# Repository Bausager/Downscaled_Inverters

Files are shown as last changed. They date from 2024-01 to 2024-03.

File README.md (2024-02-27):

# Downscaled three-phase half-bridge inverter
This project is an inverter framework for students and researches to learn, test and research state-of-the-art phase-lock-loops and control algorithms.
The inverters manly uses jellybean components, found free at the electronic laboratory for electrical engineers at Aarhus University(AU) for their students.
The purpose is to make an inexpensive and save platform instead of having to work with line voltages. 
This means all the components can be downscaled to work with 5 volt.
Here the inverter can be powered by a USB and supply its own grid.

This is an accumulative project, this means it's going to improve over time. 
There's a limited number of people working on this which means updates somethimes takes sometime.
If you want to help improve, collaborate or have something in your back pocket you want to integrate, you are very welcome to contact me!
The more the merrier!

There're some restrictions!
Since this is an open-source, student use it and research need to be understood and replicated, the code needs to be written in such a way that other prople can understand it.
Even if the person isn't an expert.
That is importent!

New fueatures waiting to be implemented can be found on the github project site [Not a Generator (NaG)](https://github.com/users/Bausager/projects/2)

## University Teaching

### Phase-Lock-Loop(PLL)
Many students at AU before this project have worked in PLLs for their bachelor thesis that meant a large part of the project was making an inverter from scratch.
This allows students not to reinvent the wheel if they are interested in other aspects than the hardware side.
With this the students can generate the grid and test their PLL on the some PCB, which lowest the bar of entre and in turn makes student projects and bachelor thesis more focused.

### Control
The students have the ability to develop control methods and test it only with a one inverter and output impedances.
Here different filter configuration or switching methods can also influence the THD which the students new have a direct way to interacting with.

### Power Factor Correction(PFC)
This PCB also allows to make it work as a PFC where control, THD and other aspects can be looked into.
Here a PFC input with a inverter output can also be pursued.

## Research Projects
Even if grid impedances does not downscale well, control algorithms, stability and many other advanced concept can be tested.
In the future, a new version of the PCB will be made for increasing the DC Link voltage to accommodate some of the downsides of the downscaled grid impedances.
As the time of writing the increase of DC Link voltage would be around 24V.
Now multiply inverters can be chained to a common grid to research stability.
Here the goal is not only to use the same micro-controller and control but to use different kinds of controls, PLLs, micro-controller, changing grid impedances, short-circuits and much more.
This will also include black start, synchronisation and much more.

## Collaborators
This project was initially an idea developed under [Associate Professor Uffe Jakobsen](https://pure.au.dk/portal/en/persons/uja%40ece.au.dk) for his classes and research into inverter control.
He also has students doing their project and bachelor thesis helping expand on this project.

A contributor [Christian Lind Vie Madsen](https://www.linkedin.com/in/christian-karl-oscar-lind-vie-madsen-11606a9b/) helps optimising written code for better performance.

And project maintainer- Me! [Michelle Bausager](https://www.linkedin.com/in/michelle-bausager/) A former student and research assistance at AU who likes to work with all aspects of inverters.

## Git Workflow.
For students or others who want to contribute, a workflow is needed to make sure everything still works in the end.
main.c on the main branch is written in such a way that every function is implementet but commented out.
This means there's a funtional implementation of every feature avaliable ready to use.

To make sure the workflow is allined a smal guide it here presented;

### Download the repository and work on an existing branch
Create of find a folder for the Git project and open your terminal in that folder.
Grab the git link and use the following git commands to download the project
```
git clone https://github.com/Bausager/Downscaled_Inverters.git
```
It’s good practice to get an overview of the project, especially the branches.
It's also here you would start if you come back to code some more!
```
git pull
git branch -a
```
There’s probably a need to code in a specific branch, if you're not in the right branch you need to select it from the list. 
Now you need to update it localy as follows:
```
git checkout specific_branch
git pull origin specific_branch
```
You can now start to make changes to the code!
To commit it, firstly you need to make sure the branch is up to date.
Then the "git add -A" commits all files and now you have to write some comments on the changes you made
Now you can push it to git!
```
git pull origin specific_branch
git add -A
git commit -m "Head line for changes
>
>
> Discription of what has been done "
git push origin specific_branch
```

### Make a new branch
Firstly make sure you have been invited to be a contributor.
Then starting working on a new feature first pull from the main branch
```
git pull origin main
```
Now you need to create a new branch where you can make your new implementations. Remember to give it a valuable name, such as "UltraCoolNewPLL".
After creating it you need to be in ýour new branch, with the opteration "checkout".
```
git branch new_branch
git checkout new_branch
```
You can now start to make changes to the code!
Since it's a new branch you don't need to make sure it's already updated as you do after you've commitet the branch for the first time.
Then the "git add -A" commits all files and now you have to write some comments on the changes you made.
```
git add -A
git commit -m "Head line for changes
>
>
> Discription of what has been done "
```
First time pushing a new branch you need to push it like this
```
git push -u origin new_branch
```
After that you can simply go to the workflow presented in *Download the repository and work on an existing branch*

### Marge branch to main
When the feature is done and tested, it's time to merge with the main branch.
This is the time and place where everything can go wrong!
Make sure main.c is steamlined like seen in the current main.c.
We're trying to implement every feature just outcommedted, that means you can just outcomment the feature to make it work.
At least that is what we're trying to do, to have a good example for the implementation for others to look at.
When we merge we need to be on the main branch.
```
git checkout main
git pull origin main
```
Now we can merge the branch into the main branch.
```
git merge new_branch
git push origin main
```
Now we’re ready to delete our branch. First we see what branches are merged, just to make sure we’re
deleting the right one. Then we delete the local branch and then the remote branch we associated with the
remote repository.
```
git branch --merged
git branch -d new_branch
git push origin --delete new_branch
```
And now it's done.

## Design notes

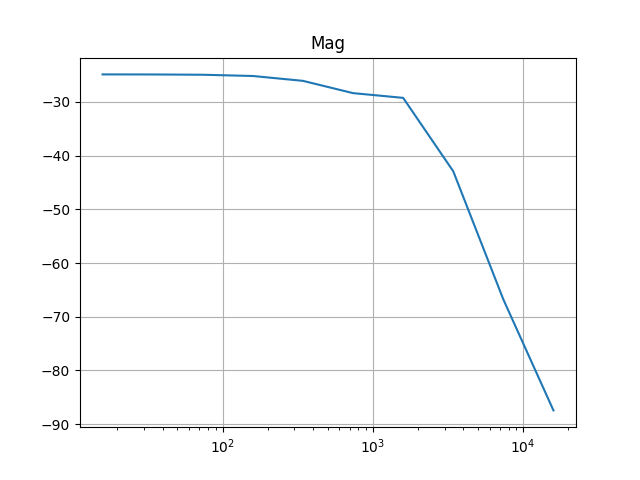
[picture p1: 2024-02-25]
Calculations/mag.png

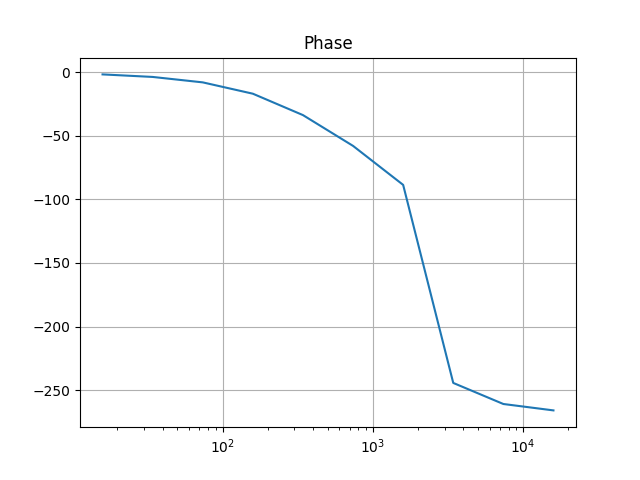
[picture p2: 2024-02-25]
Calculations/phase.png

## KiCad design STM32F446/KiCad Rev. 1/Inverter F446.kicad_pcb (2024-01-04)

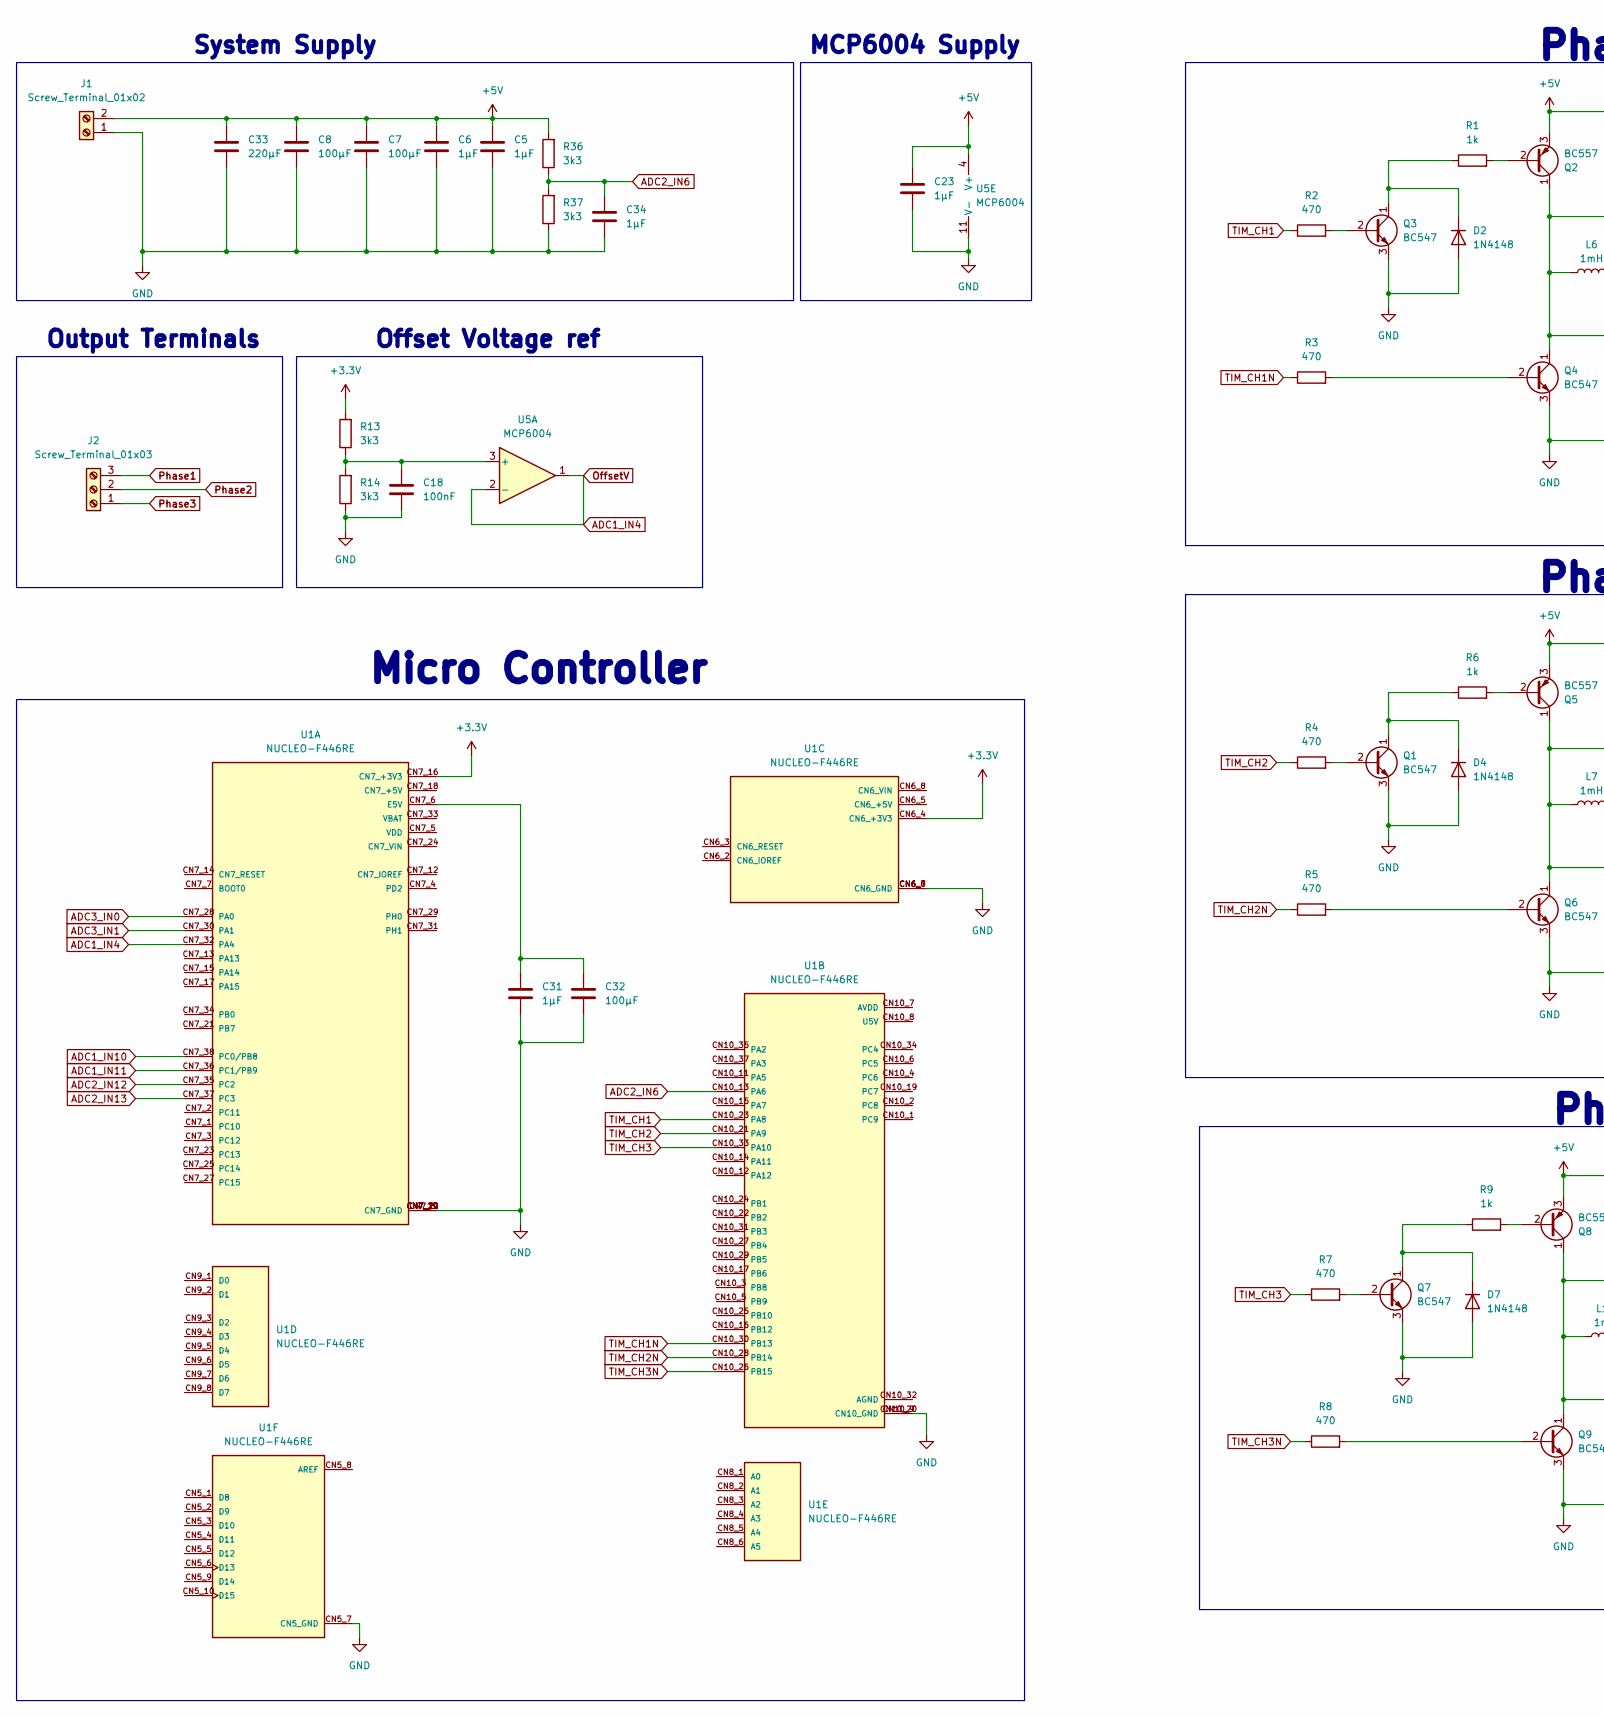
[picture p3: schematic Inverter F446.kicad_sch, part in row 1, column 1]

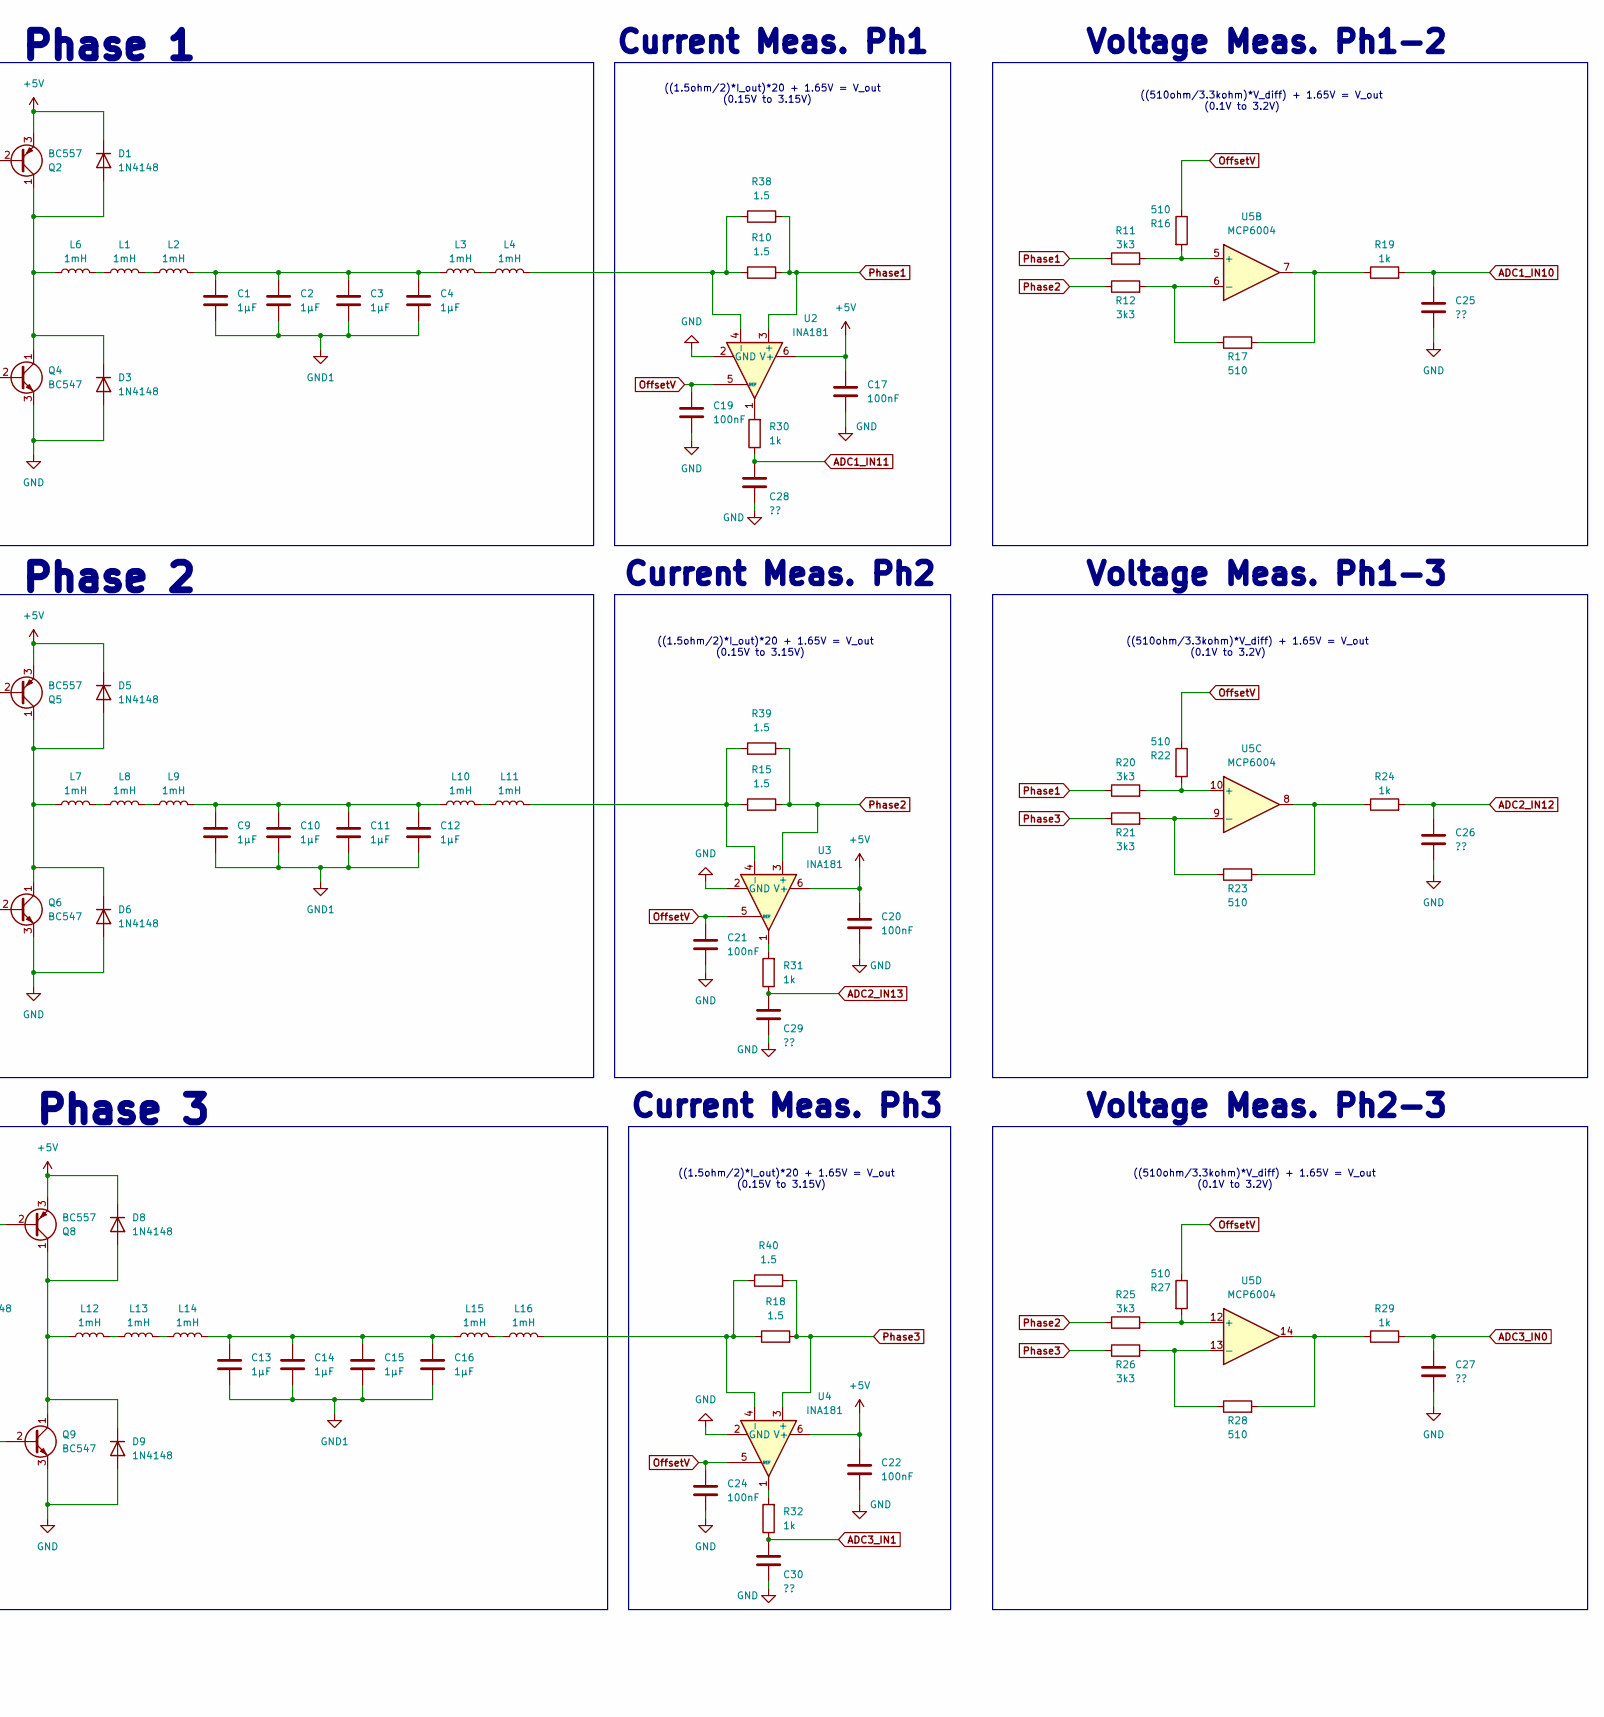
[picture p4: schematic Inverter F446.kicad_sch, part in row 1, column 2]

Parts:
C1, C2, C3, C4, C5, C6, C9, C10, C11, C12, C13, C14, C15, C16, C23, C31, C34: 1µF; C_Disc_D7.5mm_W5.0mm_P5.00mm
C7, C8, C32: 100µF; CP_Radial_D6.3mm_P2.50mm
C17, C18, C19, C20, C21, C22, C24: 100nF; C_Disc_D7.5mm_W2.5mm_P5.00mm
C25, C26, C27, C28, C29, C30: ??; C_Disc_D7.5mm_W5.0mm_P5.00mm
C33: 220µF; CP_Radial_D8.0mm_P5.00mm
D1, D2, D3, D4, D5, D6, D7, D8, D9: 1N4148; D_DO-35_SOD27_P7.62mm_Horizontal
J1: Screw_Terminal_01x02; TerminalBlock_bornier-2_P5.08mm
J2: Screw_Terminal_01x03; TerminalBlock_bornier-3_P5.08mm
L1, L2, L3, L4, L6, L7, L8, L9, L10, L11, L12, L13, L14, L15, L16: 1mH; L_Axial_L12.0mm_D5.0mm_P15.24mm_Horizontal_Fastron_MISC
Q1, Q3, Q4, Q6, Q7, Q9: BC547; TO-92_Inline
Q2, Q5, Q8: BC557; TO-92_Inline
R1, R6, R9, R19, R24, R29, R30, R31, R32: 1k; R_Axial_DIN0207_L6.3mm_D2.5mm_P10.16mm_Horizontal
R2, R3, R4, R5, R7, R8: 470; R_Axial_DIN0207_L6.3mm_D2.5mm_P10.16mm_Horizontal
R10, R15, R18, R38, R39, R40: 1.5; R_Axial_DIN0207_L6.3mm_D2.5mm_P10.16mm_Horizontal
R11, R12, R13, R14, R20, R21, R25, R26, R36, R37: 3k3; R_Axial_DIN0207_L6.3mm_D2.5mm_P10.16mm_Horizontal
R16, R17, R22, R23, R27, R28: 510; R_Axial_DIN0207_L6.3mm_D2.5mm_P10.16mm_Horizontal
U1: NUCLEO-F446RE; MODULE_NUCLEO-F446RE; PARTREV 13
U2, U3, U4: INA181; SOT-23-6
U5: MCP6004; DIP-14_W7.62mm_Socket

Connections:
+3.3V: R13.2, U1.CN6_4 (CN6_+3V3), U1.CN7_16 (CN7_+3V3)
+5V: C5.1, C6.1, C7.1, C8.1, C17.1, C20.1, C22.1, C23.1, C33.1, D1.1 (K), D5.1 (K), D8.1 (K), J1.2, Q2.3 (E), Q5.3 (E), Q8.3 (E), R36.2, U2.6 (V+), U3.6 (V+), U4.6 (V+), U5.4 (V+)
ADC1_IN4: C19.1, C21.1, C24.1, R16.1, R22.1, R27.1, U1.CN7_32 (PA4), U2.5 (REF), U3.5 (REF), U4.5 (REF), U5.1, U5.2 (-)
ADC1_IN10: C25.1, R19.2, U1.CN7_38 (PC0/PB8)
ADC1_IN11: C28.1, R30.1, U1.CN7_36 (PC1/PB9)
ADC2_IN6: C34.1, R36.1, R37.2, U1.CN10_13 (PA6)
ADC2_IN12: C26.1, R24.2, U1.CN7_35 (PC2)
ADC2_IN13: C29.1, R31.1, U1.CN7_37 (PC3)
ADC3_IN0: C27.1, R29.2, U1.CN7_28 (PA0)
ADC3_IN1: C30.1, R32.1, U1.CN7_30 (PA1)
GND: C5.2, C6.2, C7.2, C8.2, C17.2, C18.2, C19.2, C20.2, C21.2, C22.2, C23.2, C24.2, C25.2, C26.2, C27.2, C28.2, C29.2, C30.2, C31.2, C32.2, C33.2, C34.2, D2.2 (A), D3.2 (A), D4.2 (A), D6.2 (A), D7.2 (A), D9.2 (A), J1.1, Q1.3 (E), Q3.3 (E), Q4.3 (E), Q6.3 (E), Q7.3 (E), Q9.3 (E), R14.1, R37.1, U1.CN5_7 (CN5_GND), U1.CN6_6 (CN6_GND), U1.CN6_7 (CN6_GND), U1.CN7_8 (CN7_GND), U1.CN7_19 (CN7_GND), U1.CN7_20 (CN7_GND), U1.CN7_22 (CN7_GND), U1.CN10_9 (CN10_GND), U1.CN10_20 (CN10_GND), U2.2 (GND), U3.2 (GND), U4.2 (GND), U5.11 (V-)
GND1: C1.2, C2.2, C3.2, C4.2, C9.2, C10.2, C11.2, C12.2, C13.2, C14.2, C15.2, C16.2
unnamed: C1.1, C2.1, C3.1, C4.1, L2.2, L3.1
unnamed: C9.1, C10.1, C11.1, C12.1, L9.2, L10.1
unnamed: C13.1, C14.1, C15.1, C16.1, L14.2, L15.1
unnamed: D1.2 (A), D3.1 (K), L6.1, Q2.1 (C), Q4.1 (C)
unnamed: D2.1 (K), Q3.1 (C), R1.1
unnamed: D4.1 (K), Q1.1 (C), R6.1
unnamed: D5.2 (A), D6.1 (K), L7.1, Q5.1 (C), Q6.1 (C)
unnamed: D7.1 (K), Q7.1 (C), R9.1
unnamed: D8.2 (A), D9.1 (K), L12.1, Q8.1 (C), Q9.1 (C)
unnamed: L1.1, L6.2
unnamed: L1.2, L2.1
unnamed: L3.2, L4.1
unnamed: L7.2, L8.1
unnamed: L8.2, L9.1
unnamed: L10.2, L11.1
unnamed: L12.2, L13.1
unnamed: L13.2, L14.1
unnamed: L15.2, L16.1
unnamed: Q1.2 (B), R4.2
unnamed: Q2.2 (B), R1.2
unnamed: Q3.2 (B), R2.2
unnamed: Q4.2 (B), R3.2
unnamed: Q5.2 (B), R6.2
unnamed: Q6.2 (B), R5.2
unnamed: Q7.2 (B), R7.2
unnamed: Q8.2 (B), R9.2
unnamed: Q9.2 (B), R8.2
unnamed: R17.2, R19.1, U5.7
unnamed: R23.2, R24.1, U5.8
unnamed: R28.2, R29.1, U5.14
unnamed: R30.2, U2.1
unnamed: R31.2, U3.1
unnamed: R32.2, U4.1
unnamed: C31.1, C32.1, U1.CN7_6 (E5V)
unnamed: L4.2, R10.1, R38.1, U2.4 (-)
unnamed: L11.2, R15.1, R39.1, U3.4 (-)
unnamed: L16.2, R18.1, R40.1, U4.4 (-)
unnamed: C18.1, R13.1, R14.2, U5.3 (+)
unnamed: R11.2, R16.2, U5.5 (+)
unnamed: R12.2, R17.1, U5.6 (-)
unnamed: R20.2, R22.2, U5.10 (+)
unnamed: R21.2, R23.1, U5.9 (-)
unnamed: R25.2, R27.2, U5.12 (+)
unnamed: R26.2, R28.1, U5.13 (-)
Phase1: J2.3, R10.2, R11.1, R20.1, R38.2, U2.3 (+)
Phase2: J2.2, R12.1, R15.2, R25.1, R39.2, U3.3 (+)
Phase3: J2.1, R18.2, R21.1, R26.1, R40.2, U4.3 (+)
TIM_CH1: R2.1, U1.CN10_23 (PA8)
TIM_CH1N: R3.1, U1.CN10_30 (PB13)
TIM_CH2: R4.1, U1.CN10_21 (PA9)
TIM_CH2N: R5.1, U1.CN10_28 (PB14)
TIM_CH3: R7.1, U1.CN10_33 (PA10)
TIM_CH3N: R8.1, U1.CN10_26 (PB15)

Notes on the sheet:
Phase 1
Current Meas. Ph1
Current Meas. Ph3
((1.5ohm/2)*I_out)*20 + 1.65V = V_out (0.15V to 3.15V)
System Supply
Micro Controller
((510ohm/3.3kohm)*V_diff) + 1.65V = V_out (0.1V to 3.2V)
Output Terminals
Voltage Meas. Ph1-3
Voltage Meas. Ph2-3
Offset Voltage ref
Voltage Meas. Ph1-2
Phase 2
Current Meas. Ph2
Phase 3
MCP6004 Supply

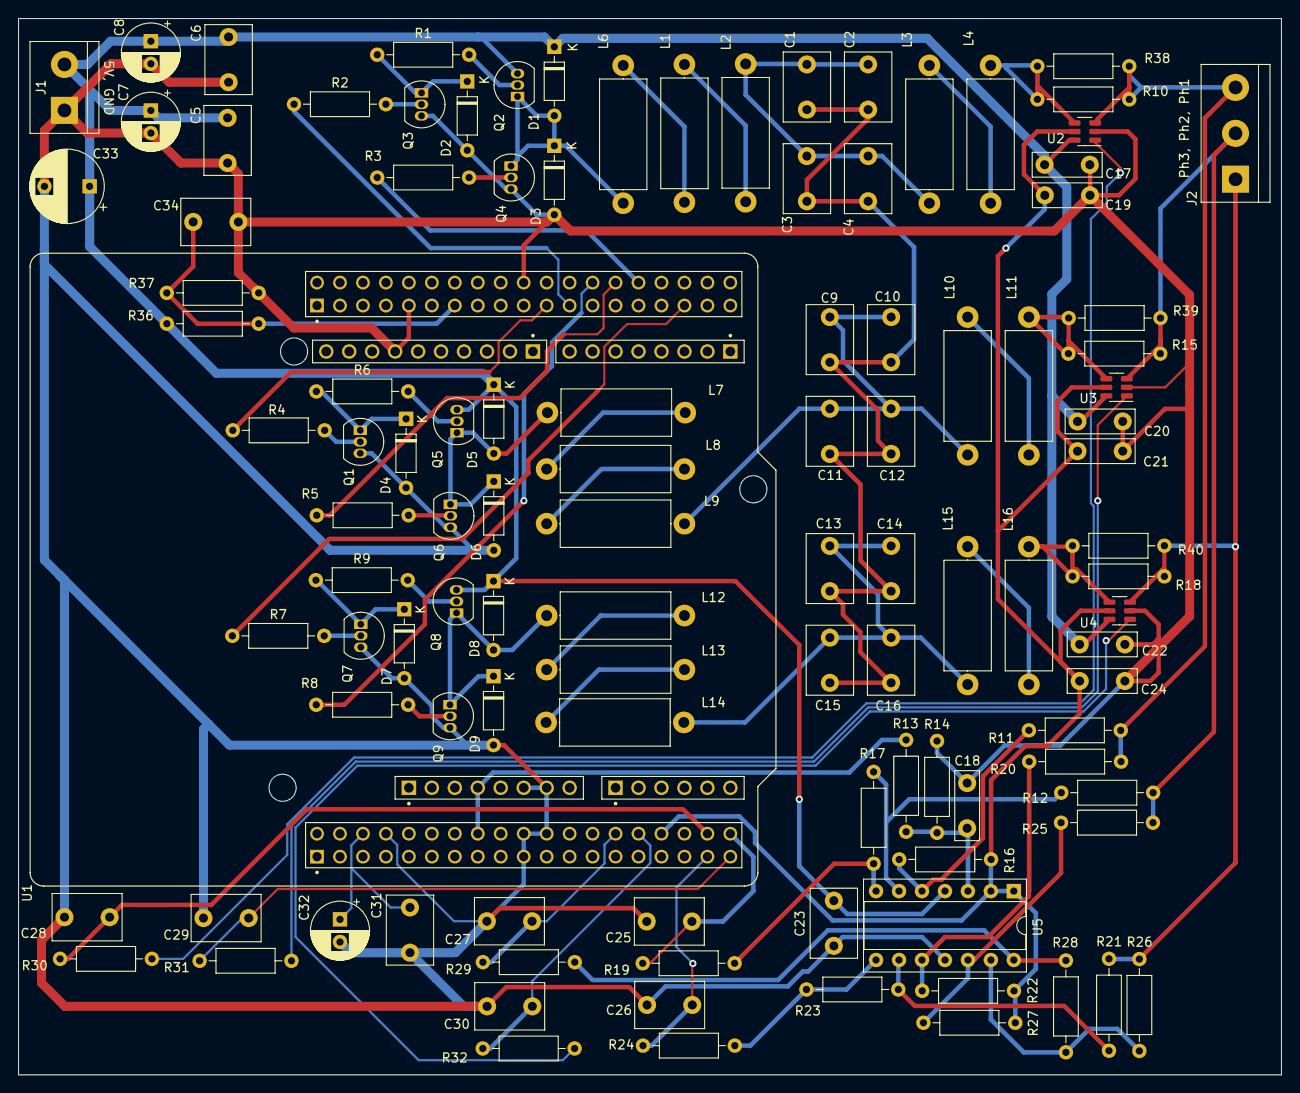
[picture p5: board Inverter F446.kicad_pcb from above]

Board: 2 copper layers, 139.7 x 116.8 mm, 111 parts (0 on the bottom side), 65 nets.

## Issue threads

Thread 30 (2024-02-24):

Upgrading Droop Control

Bausager, 2024-02-24:
Togther with Grid Estimation make a Droop Control which optimises for the grid indutance/resistance/short circuit

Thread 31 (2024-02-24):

New Inductors for LCL Filter

Bausager, 2024-02-24:
Together with better BJT or higher DC link voltages, lower parasitic resistance are needed

Bausager, 2024-02-26:
BJT or MOSFETS

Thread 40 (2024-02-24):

New PCB: DC Link reverse polarity protection

Bausager, 2024-02-24:

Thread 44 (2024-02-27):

Additional nonlinear overmodulation algorithm

Bausager, 2024-02-27:
page 93 - sec.4.2.3 for bacis info
page 98 - sec 4.2.5 for the nonlinear overmodulation algorithems
https://trinhquocnam.files.wordpress.com/2013/10/control-in-power-electronics-selected-problems.pdf

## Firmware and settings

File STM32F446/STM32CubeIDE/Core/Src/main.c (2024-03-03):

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
/* Includes ------------------------------------------------------------------*/
#include "main.h"

/* USER CODE BEGIN Includes */
#include "TimerConfig.h" // Automatic timer configuration for TIM1 and TIM2.
#include "Inverter.h" // SVM algorithm.
#include "adc_meas.h" // ADC measurements + conversations.
#include "measCalc.h" // Calculating various values.
#include "PLL.h" // PLL algorithms
#include "GridEstimation.h" // Grid estimation algorithm
#include "control.h" // For control
#include "misc.h" // For micalanius functons



#include <string.h> // Used for: sprintf(...)
#include <stdio.h> // Used for: input/output
#include <stdbool.h> // Used for: Boolean data type

//#include <stdlib.h> //

/* USER CODE END Includes */

ADC_HandleTypeDef hadc1;
ADC_HandleTypeDef hadc2;
ADC_HandleTypeDef hadc3;

TIM_HandleTypeDef htim1;
TIM_HandleTypeDef htim2;

UART_HandleTypeDef huart2;

/* USER CODE BEGIN PV */
// Switching- , Nominal grid - and Sample frequency
const float f_sw = 20e3 * 2.0f; // 20kHz for every interrupt * 2 for the whole period (20kHz switching)
const float nominal_freq = 50.0f; // Nominal grid frequency
float angular_nominal_freq = nominal_freq *2.0f * 3.1415f; // Nominal angular grid frequency (This variable is used to inject grid changes)
const float sample_freq = 5e3; // Sample frequency

// Flags
bool TIM2_falg = false; // Flag for TIM2
uint32_t TIM2_flag_acumulator = 0; // Helper for TIM2_falg (increases with every sample interrupt and resets when it hits: sample_freq)

// Control variables
float Pref, Qref, angular_freq_ref, Udref;


// Modulation index, PWM and angle variables for SVM
float Mi, angle;
float PWM1, PWM2, PWM3;

// Voltage variables
float Uab, Ubc, Uca;
float UabRMS, UbcRMS, UcaRMS;
float Ua, Ub, Uc;
float UaRMS, UbRMS, UcRMS;
float Ualpha, Ubeta, Ugamma;
float Ud, Uq, Uz;

// Current variables
float Ia, Ib, Ic;
float IaRMS, IbRMS, IcRMS;
float Ialpha, Ibeta, Igamma;
float Id, Iq, Iz;

// Power variables
float P, Q, S, Pf;

// Offset voltage for ADC and DC-Link voltage
float Offset, DCLink;

// Length of arrays
#define GridMeasNSamples 10 // Amount of stored measured samples for grid estimation
#define GridEstiNSamples 4 // Amount of estimating samples for grid estimation

// Grid Estimation
struct GridEstiMeas GridMeasValues[GridMeasNSamples]; // Stored measured samples for grid estimation
struct GridEstiVari GridEstiValues[GridEstiNSamples]; // Stored estimated samples for grid estimation

/* USER CODE END PV */

void SystemClock_Config(void);
static void MX_GPIO_Init(void);
static void MX_USART2_UART_Init(void);
static void MX_TIM1_Init(void);
static void MX_ADC1_Init(void);
static void MX_ADC2_Init(void);
static void MX_ADC3_Init(void);
static void MX_TIM2_Init(void);
/* USER CODE BEGIN 0 */
/*
 * Function for simple UART write (mainly used for simple debugging)
 */
void writeValueToUART(double value){
	char outputBuffer[256];
	uint8_t len = snprintf(outputBuffer, sizeof(outputBuffer), "Value: %f \r\n", value);
	HAL_UART_Transmit(&huart2, (uint8_t *)outputBuffer, len, 100);
}
/* USER CODE END 0 */

/**
  * @brief  The application entry point.
  * @retval int
  */
int main(void)
{
  /* MCU Configuration--------------------------------------------------------*/

  /* Reset of all peripherals, Initializes the Flash interface and the Systick. */
  HAL_Init();

  /* Configure the system clock */
  SystemClock_Config();

  /* Initialize all configured peripherals */
  MX_GPIO_Init();
  MX_USART2_UART_Init();
  MX_TIM1_Init();
  MX_ADC1_Init();
  MX_ADC2_Init();
  MX_ADC3_Init();
  MX_TIM2_Init();
  /* USER CODE BEGIN 2 */

/*
 * Starting PWM output channels
 */
  HAL_TIM_PWM_Start(&htim1, TIM_CHANNEL_1);
  HAL_TIMEx_PWMN_Start(&htim1, TIM_CHANNEL_1);
  HAL_TIM_PWM_Start(&htim1, TIM_CHANNEL_2);
  HAL_TIMEx_PWMN_Start(&htim1, TIM_CHANNEL_2);
  HAL_TIM_PWM_Start(&htim1, TIM_CHANNEL_3);
  HAL_TIMEx_PWMN_Start(&htim1, TIM_CHANNEL_3);

  /*
   * Configure timer interrupts for switching and sampling
   */
  TIM_freq(1, f_sw);
  TIM_freq(2, sample_freq);

  /*
   * Initialise SVM with timer information and interrupt frequency
   */
  svm_block_init(TIM1->ARR, f_sw);

  /*
   *  Set filter coefficients for measurements
   */
  Voltage_Filter_Length(0); // Set voltage measuring filter length
  Current_Filter_Length(0); // Set current measuring filter length
  Power_Filter_Length((uint32_t)((sample_freq/nominal_freq)*10.0f)); // Set power calculation filter length to 10 periods of nominal_freq
  RMS_Filter_Length((uint32_t)((sample_freq/nominal_freq)*10.0f)); // Set RMS filter length to 10 periods of nominal_freq

  /*
   * Initialise Grid estimation variables
   */
  InitiliseGridStruct(GridEstiNSamples, GridEstiValues);


  /*
   * Initialise Droop
   */
  Droop_Config(25.0f, 25.0f, f_sw);
  Udref = 1.9f; // 1.9V*sqrt(3) = 3.3Vpp Line-line voltage
  Pref = 0.05f; // Active Power reference for Droop control
  Qref = 0.0f; // Reactive Power reference for Droop control
  angular_freq_ref = angular_nominal_freq; // angular grid frequency reference for Droop control


  /*
   * Initialisation for Grid Following
   */
  LCL_Angle_Compensation(nominal_freq);
  dqPLL_Config(nominal_freq, sample_freq);
  AlphaBetaPLL_Config(nominal_freq, sample_freq);

  /*
   * Initialisation for Grid Forming
   */





  /*
   * Initial measurement for ADC Offset (is a must!) and DC Link voltage
   */
  for (int i = 0; i < (uint32_t)10e3; ++i) {
	  DCLink = Voltage_DCLink();
	  Offset = Voltage_Offset();
  }

  /*
   *  Start TIM1 and TIM2 Interrupts!
   */
  HAL_TIM_Base_Start_IT(&htim1);
  HAL_TIM_Base_Start_IT(&htim2);
  /* USER CODE END 2 */

  /* Infinite loop */
  /* USER CODE BEGIN WHILE */
  while (1)
  {

	  /*
	   * Runs every 1/sample_freq
	   */
	  if (TIM2_falg) {
		  TIM2_falg = false;

		  // Updates DC link voltage slow
		  Voltage_Offset();

		  /*
		   * Measure grid voltages
		   */
		  Uab = meas_Uab(Uab);
		  Ubc = meas_Ubc(Ubc);
		  Uca = meas_Uca(Uca);
		  // Re-calculate phase-phase voltages to phase-neutral voltages
		  calc_Uxx_to_Uxn(Uab, Ubc, Uca, &Ua, &Ub, &Uc);

		  /*
		   * Measure grid currents
		   */
		  Ia = meas_Ia(Ia);
		  Ib = meas_Ib(Ib);
		  Ic = meas_Ic(Ic);
		  // Calculating the Power
		  calc_Instantaneous_Power(Ua, Ub, Uc, Ia, Ib, Ic, &P, &Q);


		  // Calculate the Voltage RMS values
		  calc_RMS(Ua, Ub, Uc, &UaRMS, &UbRMS, &UcRMS);
		  calc_RMS(Uab, Ubc, Uca, &UabRMS, &UbcRMS, &UcaRMS);
		  // Calculate the Current RMS values
		  calc_RMS(Ia, Ib, Ic, &IaRMS, &IbRMS, &IcRMS);
		  // Calculating Power Factor
		  Pf = calc_Power_Factor(P, Q);

/*
		  if(TIM2_flag_acumulator < GridMeasNSamples){
			  GridMeasValues[TIM2_flag_acumulator].Pn = sqrtf(P*P);
			  GridMeasValues[TIM2_flag_acumulator].Qn = sqrtf(Q*Q);
			  GridMeasValues[TIM2_flag_acumulator].Vn = (UaRMS + UbRMS + UcRMS)/3.0f;
		  }
*/

		  /*
		   * Runs every second
		   */
		  if (TIM2_flag_acumulator >= sample_freq) {
			  TIM2_flag_acumulator = 0;

			  //transf_abc_to_dq(Ua, Ub, Uc, angle1, &Ud, &Uq);
			  //GeneticandRandomSearch(GridMeasNSamples, GridEstiNSamples, GridMeasValues, GridEstiValues);

			  char outputBuffer[256];
			  //uint8_t len = snprintf(outputBuffer, sizeof(outputBuffer), "UaRMS: %.2f. UbRMS: %.2f. UcRMS: %.2f. IaRMS: %.2f. IbRMS: %.2f. IcRMS: %.2f. P: %.2f. Q: %.2f. X: %.2f. R: %.2f. Eg: %.2f. Error: %.2f. SVM angle: %.2f. PLL angle: %.2f. Angle Error: %.2f.\r\n", UaRMS, UbRMS, UcRMS, IaRMS, IbRMS, IcRMS, P, Q, GridEstiValues[0].X, GridEstiValues[0].R, GridEstiValues[0].Eg, GridEstiValues[0].Error, angle, theta, residiual_angle);
			  uint8_t len = snprintf(outputBuffer, sizeof(outputBuffer), "UaRMS: %.2f. UbRMS: %.2f. UcRMS: %.2f. IaRMS: %.3f. IbRMS: %.3f. IcRMS: %.3f. P: %.4f. Q: %.4f. PF: %.2f. SVM angle: %.2f. Ud: %0.2f. Uq: %0.2f.\r\n", UaRMS, UbRMS, UcRMS, IaRMS, IbRMS, IcRMS, P, Q, Pf, angle, Ud, Uq);
			  HAL_UART_Transmit(&huart2, (uint8_t *)outputBuffer, len, 100);

		  }
		  TIM2_flag_acumulator++;

	  }
    /* USER CODE END WHILE */

    /* USER CODE BEGIN 3 */
  }
  /* USER CODE END 3 */
}

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
/* USER CODE BEGIN 4 */
void HAL_TIM_PeriodElapsedCallback(TIM_HandleTypeDef* htim){

	if(htim->Instance==TIM1){


		/*
		 * Grid Forming
		 */
		Droop_Forming_Resistive(P, Q, Pref, Qref, angular_nominal_freq, Udref, &angle, &Ud);
		Mi = Ud_to_Mi(DCLink, Ud);

		/*
		 * Grid Following
		 */
		//angle = dqPLL(Ua, Ub, Uc, &Ud);
		//angle = AlphaBetaPLL(Ua, Ub, Uc);


	    svm_block(Mi, angle, &PWM1, &PWM2, &PWM3);
	    TIM1->CCR1 = PWM1;
	    TIM1->CCR2 = PWM2;
	    TIM1->CCR3 = PWM3;

	}

	if(htim->Instance==TIM2){
		/*
		 * TIM2_falg to use in main-loop so it doesn't clog up the SVM.
		 */
		//char outputBuffer[256];
		//uint8_t len = snprintf(outputBuffer, sizeof(outputBuffer), "P: %.4f. Q: %.4f. Ud: %0.2f. Uq: %0.2f. Mi: %0.2f.\r\n", P, Q, Ud, Uq, Mi);
		//HAL_UART_Transmit(&huart2, (uint8_t *)outputBuffer, len, 100);
		TIM2_falg = true;
	}
}


/* USER CODE END 4 */
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


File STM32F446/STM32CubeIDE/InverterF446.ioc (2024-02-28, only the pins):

Mcu.UserName=STM32F446RETx
PA0-WKUP.Signal=ADCx_IN0
PA1.Signal=ADCx_IN1
PA10.Signal=S_TIM1_CH3
PA13.GPIO_Label=TMS
PA13.Signal=SYS_JTMS-SWDIO
PA14.GPIO_Label=TCK
PA14.Signal=SYS_JTCK-SWCLK
PA2.GPIO_Label=USART_TX
PA2.Signal=USART2_TX
PA3.GPIO_Label=USART_RX
PA3.Signal=USART2_RX
PA4.Signal=ADCx_IN4
PA5.GPIO_Label=LD2 [Green Led]
PA5.Signal=GPIO_Output
PA6.Signal=ADCx_IN6
PA8.Signal=S_TIM1_CH1
PA9.Signal=S_TIM1_CH2
PB13.Signal=TIM1_CH1N
PB14.Signal=TIM1_CH2N
PB15.Signal=TIM1_CH3N
PB3.GPIO_Label=SWO
PB3.Signal=SYS_JTDO-SWO
PC0.Signal=ADCx_IN10
PC1.Signal=ADCx_IN11
PC13.GPIO_Label=B1 [Blue PushButton]
PC13.Signal=GPXTI13
PC14-OSC32_IN.Signal=RCC_OSC32_IN
PC15-OSC32_OUT.Signal=RCC_OSC32_OUT
PC2.Signal=ADCx_IN12
PC3.Signal=ADCx_IN13
PH0-OSC_IN.Signal=RCC_OSC_IN
PH1-OSC_OUT.Signal=RCC_OSC_OUT

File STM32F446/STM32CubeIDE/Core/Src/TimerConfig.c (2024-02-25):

/*
 * TimerConfig.c
 *
 *  Created on: Dec 21, 2023
 *      Author: au467674
 */


/* Includes ------------------------------------------------------------------*/
#include "TimerConfig.h"


/*
 * Function:  TIM_freq
 * --------------------
 *	Configures Timer prescaler and auto-reload register for given timer and frequency
 *	Only work with TIM1 and TIM2
 *
 *  const uint8_t htim: Which timer is going to be configured
 *  const float Hz: Frequency of interrupts for the timer
 *
 *  returns: HAL status
 */
uint8_t TIM_freq(const uint8_t htim, const float Hz){
// Link: See page 118 for Clock tree
// https://www.st.com/resource/en/reference_manual/rm0390-stm32f446xx-advanced-armbased-32bit-mcus-stmicroelectronics.pdf

	/***  Variables ***/
	// Enums for Clock Frequencies
	enum CLK{PCLK1=0, PCLK2=1};
	// PCLK Clock Frequencies
	uint32_t PCLKx_timer_clocks[2] =  {HAL_RCC_GetPCLK1Freq(),  HAL_RCC_GetPCLK2Freq()};
	// Temporary variables
	uint32_t AutoReloadRegister_temp;
	uint16_t Prescaler_temp;
	float F_pwm, temp1, temp2;
	// Temporary variables for output frequency.
	// Needs to be initialized higher than Hz.
	float F_temp = Hz + 1.0f;
	// Max & Min Error Margin
	float Margin_Max = 1.01, Margin_Min = 0.99;

	/*** Timer 1 ***/
	//  See page 142 - RCC APB2 peripheral reset register (RCC_APB2RSTR)
	/*** Timer 1 ***/
	if (htim == 1) {
		// Finds the Timer Clock Frequency.
		if ((RCC->CFGR & RCC_CFGR_PPRE2) != 0) {
			PCLKx_timer_clocks[PCLK2] = PCLKx_timer_clocks[PCLK2]*2.0f;
		}
		// Prescaler 16-bit
		for (uint16_t Prescaler = 65535; Prescaler > 0; Prescaler--) {
			// AutoReloadRegister 16-bit
			for (uint16_t AutoReloadRegister = 0; AutoReloadRegister < 65535; AutoReloadRegister++) {
				// Calculating the Timer Frequency.
				F_pwm = (float)PCLKx_timer_clocks[PCLK2]/(((float)AutoReloadRegister + 1.0f)*((float)Prescaler + 1.0f));
				// Own abs() function.
				if ((F_temp - Hz) < 0) {
					temp1 = (F_temp - Hz) *-1;
				} else {
					temp1 = (F_temp - Hz);
				}

				if ((F_pwm - Hz) < 0) {
					temp2 = (F_pwm - Hz) *-1;
				} else {
					temp2 = (F_pwm - Hz);
				}
				// True if:
				// Calculated Frequency is close to Hz &&
				// If closer to Hz then other calculations with other prescalers.
				if ((F_pwm <= Hz) && (temp1 >= temp2) ) {
					Prescaler_temp = Prescaler;
					AutoReloadRegister_temp = AutoReloadRegister;
					F_temp = F_pwm;
					break;
				}
				// If the frequency overshoots: break.
				else if (F_pwm < Hz) {
					break;
				}
			}
		}
		// If the best found frequency is not within the margin, return: Error
		if ((F_temp > Hz*Margin_Max) || (F_temp < Hz*Margin_Min)) {
			return HAL_ERROR;
		}
		else{
			// Configure Timer with best fit & return: OK
			TIM1->PSC = Prescaler_temp;
			TIM1->ARR = AutoReloadRegister_temp;
			return HAL_OK;
		}
	}
	/*** Timer 2 ***/
	// See page 139 - RCC APB1 peripheral reset register (RCC_APB1RSTR)
	else if (htim == 2) {
		// Finds the Timer Clock Frequency.
		if ((RCC->CFGR & RCC_CFGR_PPRE1) != 0) {
			PCLKx_timer_clocks[PCLK1] = PCLKx_timer_clocks[PCLK1]*2.0f;
		}
		// Prescaler 16-bit
		for (uint16_t Prescaler = 65535; Prescaler > 0; Prescaler--) {
			// AutoReloadRegister 32-bit
			for (uint32_t AutoReloadRegister = 0; AutoReloadRegister < 4294967295; AutoReloadRegister++) {
				// Calculating the Timer Frequency.
				F_pwm = (float)PCLKx_timer_clocks[PCLK1]/(((float)AutoReloadRegister + 1.0f)*((float)Prescaler + 1.0f));
				// Own abs() function.
				if ((F_temp - Hz) < 0) {
					temp1 = (F_temp - Hz) *-1;
				} else {
					temp1 = (F_temp - Hz);
				}
				if ((F_pwm - Hz) < 0) {
					temp2 = (F_pwm - Hz) *-1;
				} else {
					temp2 = (F_pwm - Hz);
				}

				// True if:
				// Calculated Frequency is close to Hz &&
				// If closer to Hz then other calculations with other prescalers.
				if ((F_pwm <= Hz) && (temp1 >= temp2) ) {
					Prescaler_temp = Prescaler;
					AutoReloadRegister_temp = AutoReloadRegister;
					F_temp = F_pwm;
					break;
				}
				// If the frequency overshoots: break.
				else if (F_pwm < Hz) {
					break;
				}
			}
		}

		// If the best found frequency is not within the margin, return: Error
		if ((F_temp > Hz*Margin_Max) || (F_temp < Hz*Margin_Min)) {

			return HAL_ERROR;
		}
		else{
			// Configure Timer with best fit & return: OK
			TIM2->PSC = Prescaler_temp;
			TIM2->ARR = AutoReloadRegister_temp;
			return HAL_OK;
		}
	}
	return HAL_ERROR;
}

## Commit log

2023-12-25 Initial Work
    [Inverter F446.kicad_pcb, Inverter F446.kicad_sch]
2023-12-30 PWM and ADC tested
2024-01-01 Folder cleanup
    [Inverter F446.kicad_pcb, Inverter F446.kicad_sch]
2024-01-01 PCB makeing
    [Inverter F446.kicad_sch]
2024-01-02 PCB Placement Done
    [Inverter F446.kicad_pcb, Inverter F446.kicad_sch]
2024-01-03 A bit of clean-up
    [Inverter F446.kicad_pcb, Inverter F446.kicad_sch]
2024-01-04 First Routing
    [Inverter F446.kicad_pcb]
2024-01-04 Generated Gaber files
    [Inverter F446-B_Cu.gbr, Inverter F446-B_Mask.gbr, Inverter F446-B_Paste.gbr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]
2024-02-15 Intantaniu Power calculation is done.
2024-02-18 Grid Estimator doesn't work yet
    [GridEstimation.c, InverterF446.ioc, PLL.c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]
2024-02-21 Comments, test case in main and cleanup
2024-02-22 Something is wrong with the power calculations and measurement calc
    [Inverter.c, adc_meas.c, main.c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]
2024-02-24 Cleanup and Commenting
    All is more or less clean up with comments and referances to used material, articles and pattens.
2024-02-25 Const for input variables
    Fixed so every input for functions are const, every output is ether a pointer or a return.
    This makes it esaier to see what is the function input and outputs
    [GridEstimation.c, Inverter.c, Inverter.h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]
2024-02-25 LCL Phase compensation is done
    LCL phaseshift is calculated and integrated into dqPLL for angle compensation
    Since I'm an idiot i've also fixed some of the problems with the dqPLL.
    Now the PI coeff are calculated correctly
    I used the grid frequency before. I now use the angular grid frequency and it seems more stable
    #SundayWork
    [PLL.c, adc_meas.c, main.c]
2024-02-26 AlphaBetaPLL and more
    I've gotten the AlphaBetaPLL to work. But there's still something about the LCL anlge compensaton.
    [Inverter F446-B_Cu.gbr, Inverter F446-B_Mask.gbr, Inverter F446-B_Paste.gbr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]
2024-02-28 Fixed minor error in SVM block
    [Inverter.c, InverterF446.ioc, main.c]
2024-03-03 Droop Control on Resistive grid (formning)
    Not commented yet but works

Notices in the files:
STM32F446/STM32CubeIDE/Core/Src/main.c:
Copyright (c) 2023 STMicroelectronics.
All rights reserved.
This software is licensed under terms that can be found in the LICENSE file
